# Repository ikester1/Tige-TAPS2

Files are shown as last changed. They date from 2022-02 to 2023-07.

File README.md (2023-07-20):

# Replacement Tige TAPS Trim Controller

This is a replacement for the original trim controller for an early 2000's [Tige](https://www.tige.com/) 22v wakeboard boat.
The *electric actuator* is made by [Lenco](https://www.lencomarine.com), the Tige logo'd
trim indicator gauge is probably made by [Faria](https://fariabeede.com), and the
"black box" controller is under the dashboard.  The "black box" takes the trim switch input and drives the actuator
and gauge.  Coupled with a plate on the transom, Tige called the entire system **TAPS2**.

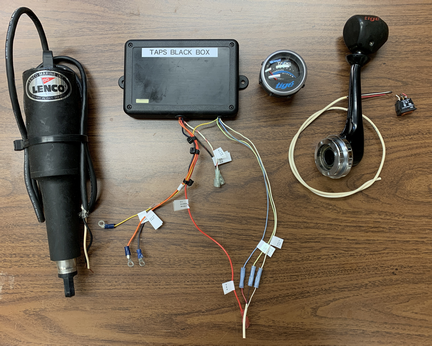
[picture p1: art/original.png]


The original controller is prone to failure, and is no longer available from Lenco or Tige.  There are
other solutions from Lenco but there are none which retain the use of the original trim switch and Tige
gauge.

Tige's TAPS controller fully retracts the actuator at each start so one must
reposition the trim at every restart.
This project improves on the original implementation by saving the final actuator position for the next
restart.
If everything works right, the trim will not move and the gauge will be correctly positioned when the
boat is restarted.

The controller's external connections are power and ground, trim switch top/middle/bottom,
gauge power/ground/signal, and two actuator motor power leads.  The controller box has a lighted
setup pushbutton and redundant trim switch.
The box, while deeper than the original controller, has the same footprint.

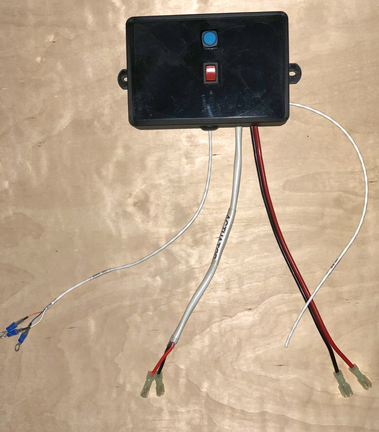
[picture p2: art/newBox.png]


This project includes the controller's schematic diagram and PCB layout, a 3D printable enclosure, and the C++
controller software.  With access to a 3D printer, the cost of the controller should be less than $75.

# Making the Controller

The replacement controller is a custom processor board connected to a commercial
[H-Bridge](https://en.wikipedia.org/wiki/H-bridge)
to switch the relatively high current actuator connections.
The processor board holds a [Raspberry Pi Pico](https://www.google.com/search?q=raspberry+pico) and surrounding
glue circuitry.

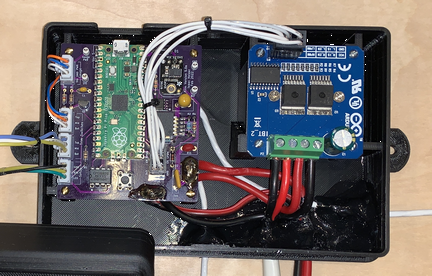
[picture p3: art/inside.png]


## Processor Board

The [pcb](pcb) directory holds the [KiCad 6](https://www.kicad.org/) files detailing the schematic and
printed circuit layout, and
[bin/TAPS.zip](bin)
is a
[Gerber](https://en.wikipedia.org/wiki/Gerber_format)
file to send to a printed circuit board
fabricator such as [OSHPARK](https://oshpark.com/).

Almost all components are available at [Digi-Key](https://www.digikey.com/) and the schematic is annotated with
manufacturer and product numbers for each component.
The Pico power supply is from [adafruit](https://www.adafruit.com/product/4683).
In addition to the usual soldering supplies, a special crimper
( [Amazon](https://www.amazon.com/dp/B088NQV8Z3) )
is needed for the board's connectors though
one could skip the connectors and solder the wires to the boards.

## H-Bridge

The commercial H-Bridge is a BTS7960 43A High Power Motor Driver Module and can be purchased on Amazon for less than $10 from
[several souces](https://www.amazon.com/s/?url=search-alias%3Daps&field-keywords=BTS7960+43A+Motor+Driver+Module).
The H-Bridge board has an 8 pin header for its logic connections to the processor board; replace this header with the same locking connector
as the processor board to improve robustness.

## Code

The C++ code is compiled on Linux with the [Raspberry Pi Pico C/C++ SDK](https://datasheets.raspberrypi.com/pico/raspberry-pi-pico-c-sdk.pdf).
Go to the [src](src) directory, type `cmake -B build` followed by `cd build && make` to generate the executable to
copy to the Pico processor as described in the SDK. The most recent executable is [bin/taps.elf](bin).

## Enclosure and Switches

The [box](box) directory holds the [SketchUp](https://www.sketchup.com/) enclosure design files.
[Cura](https://ultimaker.com/software/ultimaker-cura) successfully slices
[bin/boxBottom.stl](bin) and [bin/boxTop.stl](bin)
for an [Ultimaker 3D printer](https://ultimaker.com/) though other slicers and printers should work.
The ABS enclosure's bottom secures the boards and external wires with 2-56 screws, while the top holds the setup button and
auxiliary trim switch.
The auxiliary trim switch is a duplicate of the button used on the throttle of the Tige boat.
It is manufactured by
[E-Switch](https://www.e-switch.com/),
part number
R1966IBLKREDEF,
and available on
[Digi-Key](https://www.digikey.com/short/t0br9zjr)
as part number [EG5445-ND](https://www.digikey.com/short/t0br9zjr).
The 16mm illumated setup pushbutton is available from [adafruit](https://www.adafruit.com/product/1477)
and [amazon](https://www.amazon.com/dp/B0148183D2).

The box top and bottom are held together with two 6.3mm automotive plastic trim fasteners.

## Connections

Connect the three *gauge* wires to the existing Tige TAPS gauge -- these should be the only wires connected to
the gauge terminal posts.  This new black box supplies power to the gauge; **do not** also connect the gauge's power terminal to
the boat's electrical system.  Looking from the rear, the black box gauge *PWR* leads goes on the right, *GND* goes in the middle,
and *SIG* goes on the left.  **Connecting any power lead to the gauge's *SIG* terminal will damage the gauge.**
The spade terminal near the blue cap is for gauge illumination and this connection should go to the lighting circuit
shared with the other instruments.

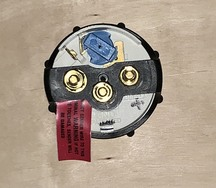
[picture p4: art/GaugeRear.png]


Connect the black box's two actuator leads to the two leads coming from the Lenco electric actuator.  Polarity
is only important when it comes time to ensure the actuator retracts when the black box thinks it should be
retracting, and extends when the black box thinks it is extending the actuator.  If you get the leads backwards,
they can simply be plugged in the other way.

Connect the three trim switch wires to the boat's trim switch ... on my boat this switch is on the throttle handle.
There is no appreciable current flowing through the trim switch so any secure means of connection (any kind of connector)
should be fine.  Do not otherwise connect the boat's power or ground to these connections.

Finally, connect the black box's power and ground to the electrical system.  The heavy power lead should be connected, most likely,
to the same 15A breaker that was powering the original black box (actually, a 10A breaker is probably adequate).
The other, lighter, power lead should be connected to a switched power source.

# Setup

The black box has a *setup mode* entered by pressing its pushbutton.  The button's LED pulses
when the box is in *setup mode* and goes dark when *setup mode* is exited.  *Setup mode* is automatically exited after one
minute of inactivity, or if the pushbutton is pressed and held for at least two seconds.

As soon as *setup mode* is entered, the actuator should fully retract.
If the actuator extends instead of retracts, simply reverse the actuator leads and try again.
When not in
*setup mode*, pressing the side
of the rocker switch nearest the pushbutton should extend the actuator, the other side of
the rocker switch should retract it.
Similarly, pressing the top of the rocker switch on the throttle should extend the actuator and the bottom half of the
switch should retract it.  Something is wrong with the
throttle's switch or wiring if the box's rocker switch works but the throttle's does not.

The primary purpose of *setup mode* is to calibrate the TAPS gauge.
This is done by manually setting the gauge's fully retracted (wakeboard) and 25% - 50% - 75% - 100% 
extended (slalom) gauge needle positions.
More specifically, the gauge's 8, 6, 4, 2, and 0 readings are adjusted.
Enter *setup mode* to adjust these positions and use the trim switch to set the needle's **8** position.
Press the setup button and set the needle's **6** position.
Press the button and set the **4** position; continue for the **2** and **0** positions.
One should be careful when setting the **0** position: release the trim switch as soon as the
**0** position is reached (do not linger) as doing otherwise will bias the box's idea of when **0** was reached.
*Setup mode* automatically exits once the setup button is pressed after adjusting for the **0** position.

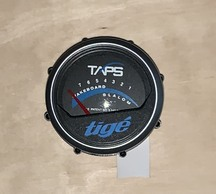
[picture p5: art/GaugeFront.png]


# Operation

The trim switch and TAPS system should operate exactly as the original system, except:
- The new black box remembers the actuator and gauge positions when the boat is shut down.
The original box retracts the actuator and resets the gauge at every boat restart.

- The original black box runs the actuator as long as the trim switch is pressed; this replacement box stops the actuator
once it is 50% beyond the retract or extend limits.
In any case, running the Lenco actuator beyond its limits causes no harm to the actuator.

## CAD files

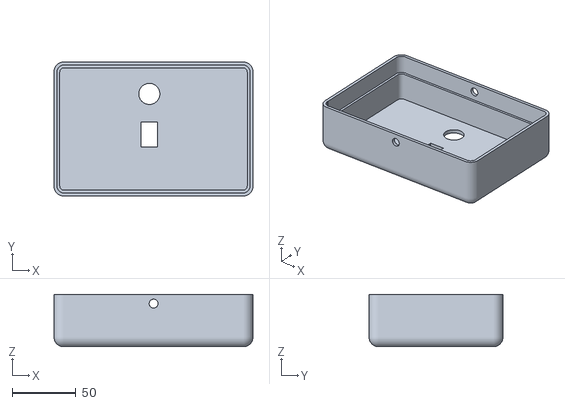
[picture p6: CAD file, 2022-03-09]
bin/boxTop.stl
156.0 x 105.0 x 41.1

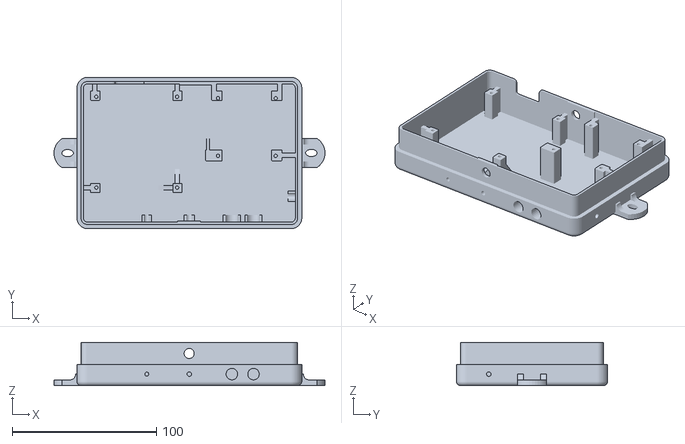
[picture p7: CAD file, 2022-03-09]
bin/boxBottom.stl
187.9 x 105.0 x 30.0

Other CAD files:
box/box.skp

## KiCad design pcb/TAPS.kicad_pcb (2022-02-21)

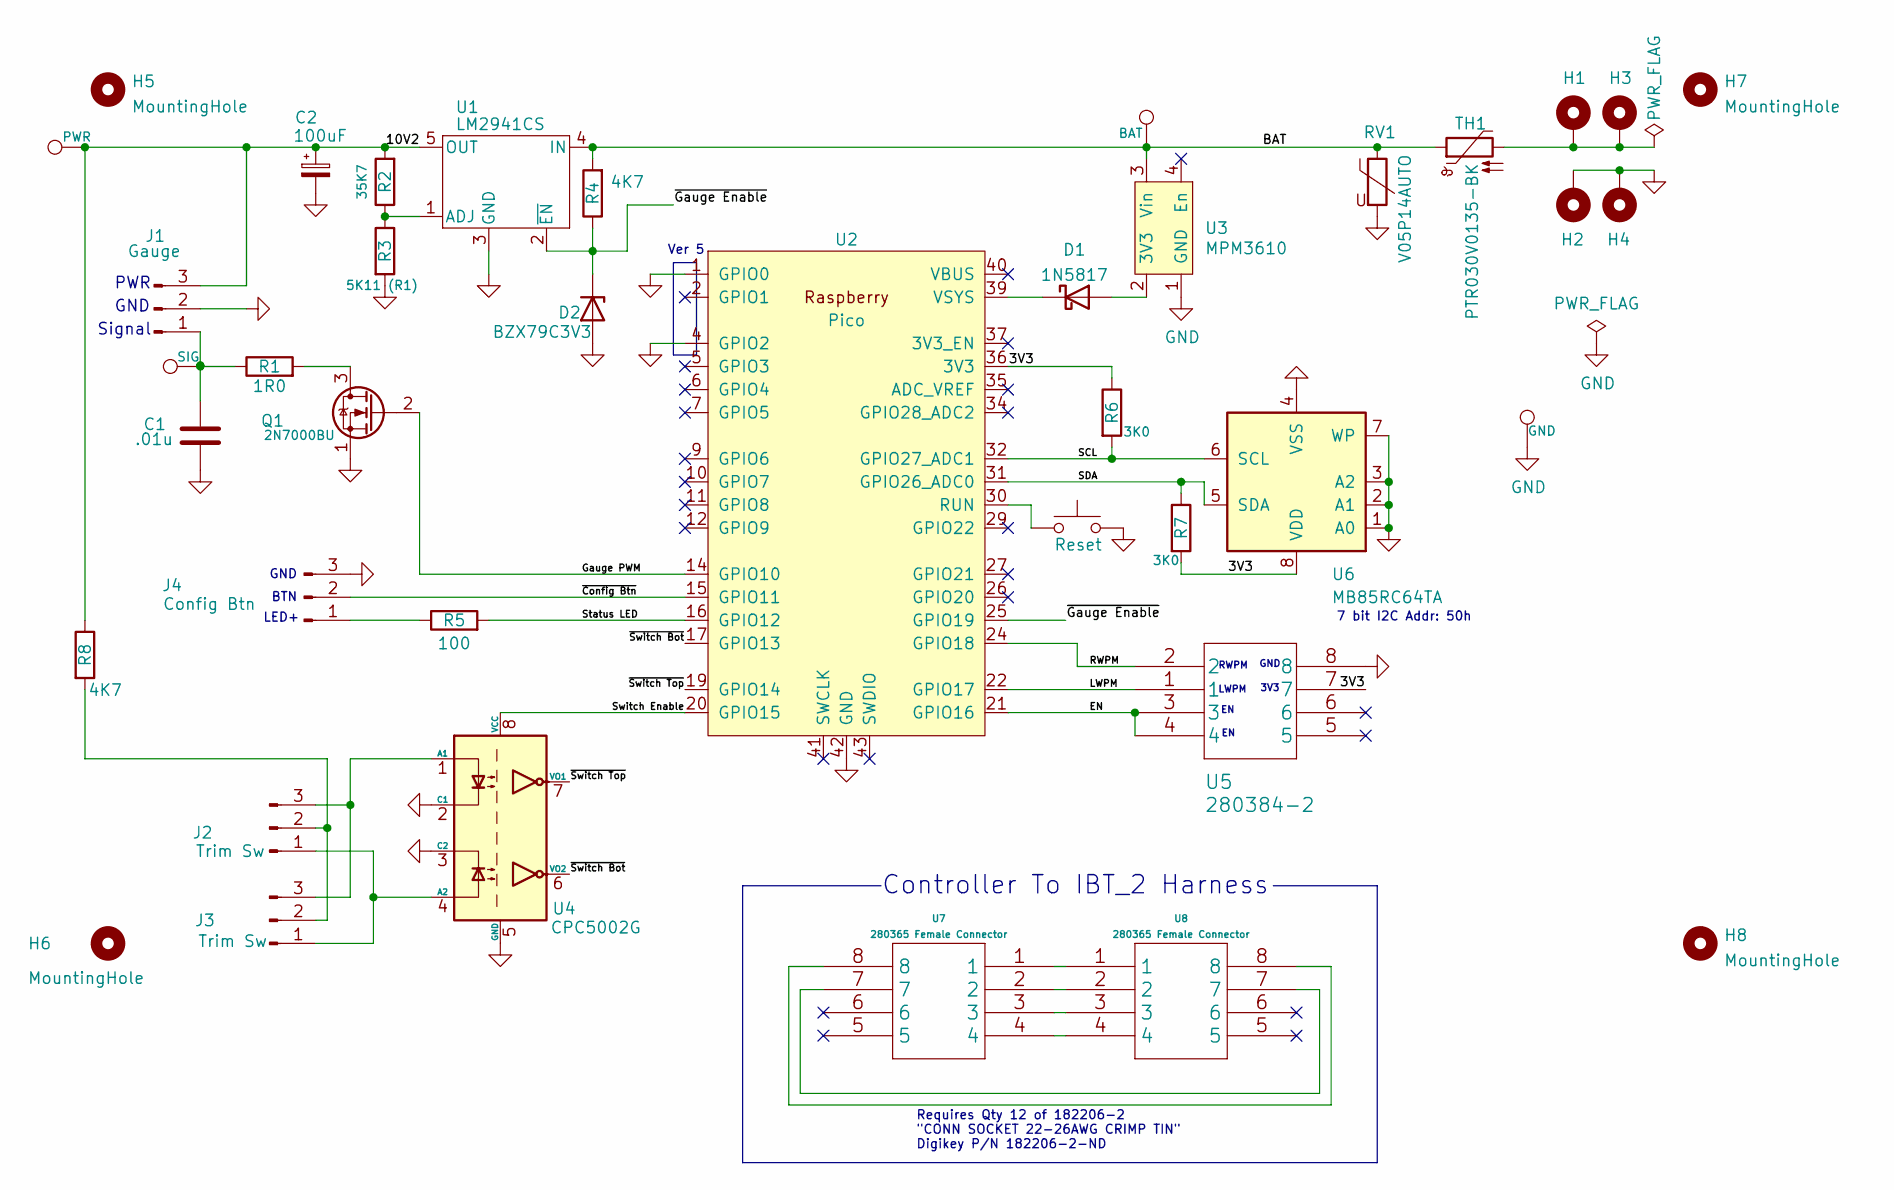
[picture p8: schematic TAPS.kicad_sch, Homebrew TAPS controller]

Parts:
C1: .01u; C_Disc_D4.3mm_W1.9mm_P5.00mm; Digikey PN 399-4206-ND
C2: 100uF; C_Disc_D9.0mm_W5.0mm_P5.00mm; Digikey PN 478-1847-ND
D1: 1N5817; D_A-405_P7.62mm_Horizontal; Digikey PN 1N5817RLGOSCT-ND
D2: BZX79C3V3; D_DO-34_SOD68_P7.62mm_Horizontal; Digikey PN BZX79C3V3-ND
H1, H2, H3, H4: MountingHole_Pad; MountingHole_2.5mm_Pad_TopBottom
H5, H6, H7, H8: MountingHole; MountingHole_2.5mm
J1: Gauge; JST_XH_B3B-XH-A_1x03_P2.50mm_Vertical; Digikey PN 455-1990-ND
J2, J3: Trim Sw; JST_XH_B3B-XH-A_1x03_P2.50mm_Vertical; Digikey PN 455-1990-ND
J4: Config Btn; JST_XH_B3B-XH-A_1x03_P2.50mm_Vertical
Q1: 2N7000BU; TO-92_Inline; Digikey PN 2N7000BU-ND
R1: 1R0; R_Axial_DIN0204_L3.6mm_D1.6mm_P7.62mm_Horizontal; Digikey PN CF18JT1R00CT-ND
R2: 35K7; R_Axial_DIN0204_L3.6mm_D1.6mm_P7.62mm_Horizontal; Digikey PN RNF18FTD35K7CT-ND
R3: 5K11 (R1); R_Axial_DIN0204_L3.6mm_D1.6mm_P7.62mm_Horizontal; Digikey PN 738-RNF18FTD5K11CT-ND
R4, R8: 4K7; R_Axial_DIN0204_L3.6mm_D1.6mm_P7.62mm_Horizontal; Digikey PN CF18JT4K70CT-ND
R5: 100; R_Axial_DIN0204_L3.6mm_D1.6mm_P7.62mm_Horizontal; Digikey PN CF18JT100RCT-ND
R6, R7: 3K0; R_Axial_DIN0204_L3.6mm_D1.6mm_P7.62mm_Horizontal; Digikey PN CF18JT3K00CT-ND
RV1: V05P14AUTO; C_Disc_D7.5mm_W5.0mm_P5.00mm; Digikey PN F6411-ND
SW1: Reset; SW_PUSH_6mm_H7.3mm; Digikey PN 450-1650-ND
TH1: PTR030V0135-BK; C_Disc_D10.0mm_W2.5mm_P5.00mm; Digikey PN PTR030V0135-BK-ND
TP1: PWR; TestPoint_Keystone_5000-5004_Miniature; Digikey PN 36-5002-ND
TP2: BAT; TestPoint_Keystone_5000-5004_Miniature; Digikey PN 36-5002-ND
TP3: GND; TestPoint_Keystone_5000-5004_Miniature; Digikey PN 36-5002-ND
TP4: SIG; TestPoint_Keystone_5000-5004_Miniature; Digikey PN 36-5002-ND
U1: LM2941CS; TO-263-5_TabPin3; Digikey PN LM2941CS-ND
U2: Pico; RPi_Pico_SMD; Digikey PN 2648-SC0915CT-ND
U3: MPM3610; Converter_DCDC_Adafruit_MPM3610
U4: CPC5002G; DIP-8_W7.62mm; Digikey PN CLA383-ND
U5: 280384-2; Connector_TE_280384-2; Digikey PN A106409-ND
U6: MB85RC64TA; SOP-8_3.9x4.9mm_P1.27mm; Digikey PN 865-1274-1-ND
U7, U8: 280365 Female Connector; Digikey PN A121748-ND

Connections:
/3V3: R6.1, R7.2, U2.36 (3V3), U5.7, U6.8 (VDD)
/10V2: C2.1, J1.3, R2.2, R8.1, TP1.1, U1.5 (OUT)
/BAT: R4.2, RV1.1, TH1.1, TP2.1, U1.4 (IN), U3.3 (Vin)
/EN: U2.21 (GPIO16), U5.3, U5.4
/Gauge PWM: Q1.2 (G), U2.14 (GPIO10)
/LWPM: U2.22 (GPIO17), U5.1
/RWPM: U2.24 (GPIO18), U5.2
/SCL: R6.2, U2.32 (GPIO27_ADC1), U6.6 (SCL)
/SDA: R7.1, U2.31 (GPIO26_ADC0), U6.5 (SDA)
/Status LED: R5.2, U2.16 (GPIO12)
/Switch Enable: U2.20 (GPIO15), U4.8 (VCC)
/~Config Btn: J4.2, U2.15 (GPIO11)
/~Gauge Enable: D2.1 (K), R4.1, U1.2 (~EN), U2.25 (GPIO19)
/~Switch Bot: U2.17 (GPIO13), U4.6 (VO2)
/~Switch Top: U2.19 (GPIO14), U4.7 (VO1)
GND: C1.2, C2.2, D2.2 (A), H2.1, H4.1, J1.2, J4.3, Q1.1 (S), R3.2, RV1.2, SW1.2, TP3.1, U1.3 (GND), U2.1 (GPIO0), U2.3 (GND), U2.4 (GPIO2), U2.8 (GND), U2.13 (GND), U2.18 (GND), U2.23 (GND), U2.28 (GND), U2.33 (GND), U2.38 (GND), U2.42 (GND), U3.1 (GND), U4.2 (C1), U4.3 (C2), U4.5 (GND), U5.8, U6.1 (A0), U6.2 (A1), U6.3 (A2), U6.4 (VSS), U6.7 (WP)
unnamed: C1.1, J1.1, R1.1, TP4.1
unnamed: D1.1 (K), U2.39 (VSYS)
unnamed: D1.2 (A), U3.2 (3V3)
unnamed: H1.1, H3.1, TH1.2
unnamed: J2.1, J3.1, U4.4 (A2)
unnamed: J2.2, J3.2, R8.2
unnamed: J2.3, J3.3, U4.1 (A1)
unnamed: J4.1, R5.1
unnamed: Q1.3 (D), R1.2
unnamed: R2.1, R3.1, U1.1 (ADJ)
unnamed: SW1.1, U2.30 (RUN)
unnamed: U7.1, U8.1
unnamed: U7.2, U8.2
unnamed: U7.3, U8.3
unnamed: U7.4, U8.4
unnamed: U7.7, U8.7
unnamed: U7.8, U8.8

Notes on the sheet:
Signal
3V3
7 bit I2C Addr: 50h
RWPM
BTN
Requires Qty 12 of 182206-2 "CONN SOCKET 22-26AWG CRIMP TIN" Digikey P/N 182206-2-ND
GND
Ver 5
LED+
LWPM
Controller To IBT_2 Harness
PWR

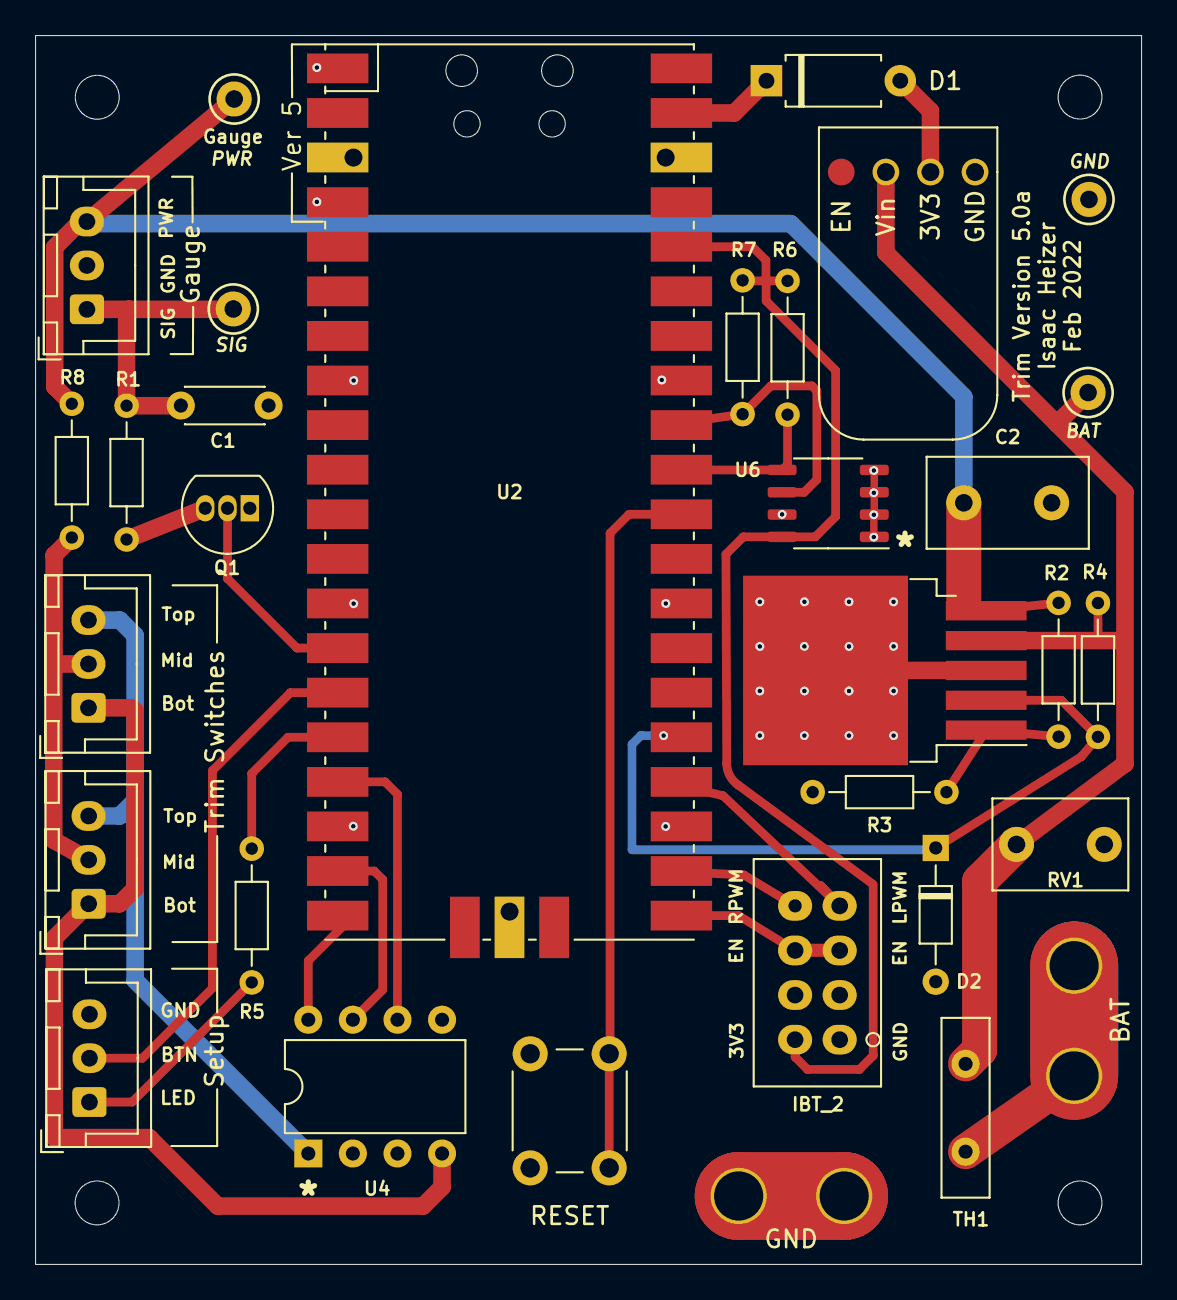
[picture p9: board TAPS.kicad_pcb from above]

Board: 2 copper layers, 63.0 x 70.0 mm, 38 parts (0 on the bottom side), 27 nets.

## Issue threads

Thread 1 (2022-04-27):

Bottom Silkscreen

matthewmooney, 2022-04-27:
Thank you for putting this together!  Exactly what I need for my 04 Tige 24V.  Attempting to get the board printed with OSHPark but I keep getting an error that the zip file is missing the bottom silkscreen.

ikester1, 2022-04-27:
There is no bottom silkscreen!  OSH used to be OK with that….

I made three extra units.  I’ll send you one for $50 to cover costs and
labor if you want.  Buyer beware, though!

Mooney pilot?  I built and flew a Lancair

On Wed, Apr 27, 2022 at 12:28 PM matthewmooney ***@***.***>
wrote:

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
--
Sent from my iPad

matthewmooney, 2022-04-28:
There might be a way to navigate it but I figured I would start by seeing if maybe it got left out on accident.  If you have a completed board i would gladly take that off your hands.   It would save me a lot of headaches! 

Unfortunately no just the last name,   however I'm hoping to go back to school to become a pilot in the fall. 

⁣Get BlueMail for Android

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

Closed 2023-07-10.

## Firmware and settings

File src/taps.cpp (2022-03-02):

#include <stdio.h>
#include <memory.h>
#include "pico/stdlib.h"

#include <cmath>

#include "config.h"
#include "util.hpp"
#include "CGauge.hpp"
#include "CNVFlash.hpp"
#include "CNVFRAM.hpp"
#include "taps.hpp"
#include "CActuator.hpp"
#include "CPowerFail.hpp"

void configure( CNVState&, CLED& statusLED, CButton& button, CSPDT& trimSwitch, CActuator&, CGauge& );
void demoMode( CGauge&, CButton& stopButton );
void doCommand( int ch, CNVState& );

static CNVState& findNVResource() {
    static CNVFRAM nvFRAM( I2C_ADDR::FRAM, BoardPin::FRAM_SDA );
    if( nvFRAM.size() > 0 )
        return nvFRAM;

    static CNVFlash nvFlash;
    return nvFlash;
}

int main()
{
    stdio_init_all();

    CNVState&   nvState = findNVResource();
    CLED        picoLED( BoardPin::STANDARD_LED );
    CLED        statusLED( BoardPin::STATUS_LED );
    CPowerFail  powerFail;
    CActuator   actuator( ACTUATOR_FULL_TRANSIT_MS );
    CGauge      gauge( nvState.gaugeCal().get(), GAUGE_PWM_FREQ );

    bool        movedTrimSinceLastSave = false;
    int         numberOfTrimMovements  = 0;

    //
    // This object posts "TRIM_SWITCH_xxx" messages as the trim switch is manipulated
    //
    class trimSwitch : public CSPDT {
        typedef CSPDT   super;
        CGPIO_OUT       m_switchEnable;     //  Must be set to output high on boards with optical switch isolators
    public:
        trimSwitch() :
        super( BoardPin::TRIM_SWITCH_EXTEND, BoardPin::TRIM_SWITCH_RETRACT ),
        m_switchEnable( BoardPin::TRIM_SWITCH_ENABLE )
        {
            m_switchEnable.setOn();
        }

        void onTop(bool pressed) {
            if( auto msg = CMessage::alloc( pressed ? CMessage::Type::TRIM_TOP_ON : CMessage::Type::TRIM_OFF ) )
                msg->push();
        }
        void onBottom(bool pressed) {
            if( auto msg = CMessage::alloc( pressed ? CMessage::Type::TRIM_BOTTOM_ON : CMessage::Type::TRIM_OFF ) )
                msg->push();
        }
    } spdt;

    //
    // This object posts a "CONFIG_BUTTON_ON" message when the configure pushbutton is pressed
    //
    class ConfigButton : public CButton {
        typedef     CButton super;
        bool        m_messages;
    public:
        ConfigButton() : super( BoardPin::CONFIG_PUSHBUTTON ), m_messages( false )  {}
        void onChange( bool b ) override {
            if( b && m_messages )
                if( auto msg = CMessage::alloc( CMessage::Type::CONFIG_BUTTON_ON ) )
                    msg->push();
        }
        void enableMessages()       { super::enable(); m_messages = true; }
        void disableMessages()      { m_messages = false; }
    } configButton;
    configButton.enable();          // no messages yet

    //
    // This object posts a "HEARTBEAT" message once per second, and blinks the pico led
    //
    class heartBeat {
        struct myTick : public CGlobalTimer::COnTick {
            heartBeat &m_me;
            void onTick() override                      { m_me.onTick(); }
            myTick( heartBeat &m ) : m_me( m )          {}
        } m_myTick;

        const int   m_interval;
        int         m_count;
        CLED        &m_led;                 // LED to toggle every m_interval
        bool        m_msg;                  // should we send message at m_interval?

    public:
        heartBeat( int interval, CLED& led ) : m_myTick(*this), m_interval( interval ), m_count(0), m_led(led), m_msg(false) {}
        void onTick()           {   if( --m_count <= 0 ) {
                                        m_led.toggle();
                                        m_count = m_interval;
                                        if( m_msg )
                                            if( auto msg = CMessage::alloc( CMessage::Type::HEARTBEAT ) )
                                                msg->push();
                                    }
        
                                };

        bool enableMessages()           { auto oval = m_msg; m_msg = true; m_myTick.start(); return oval; }
        bool disableMessages()          { auto oval = m_msg; m_msg = false; return oval; }

    } heartBeat( 1000/CGlobalTimer::msPerTick(), picoLED );

    gauge.enable();

    if( configButton.strobe() == true ) {
        //
        // Config button is pressed during power up....enter demo mode which sweeps the gauge dial
        //
        configButton.waitForPressed();
        demoMode( gauge, configButton );
    }

    float recoveredActuatorPercent = NAN;
    if( nvState.reason().wasValid() && nvState.actuatorPercent().wasValid() ) {
        if( nvState.reason().get() == CNVState::PowerDownSave || nvState.reason().get() == CNVState::SavedPositionImmediate ) {
            //
            // We were able to save and recover the last actuator postion, so we assume it is still at that position.
            //   All we need to do is let the actuator know where it is
            //
            recoveredActuatorPercent = nvState.actuatorPercent().get();
            actuator.setAlreadyAtPercent( recoveredActuatorPercent );
            spdt.enable();
            configButton.enableMessages();
            gauge.setSlow( 100 );
        }
    }

    if( isnan( recoveredActuatorPercent ) ) {
        //
        // Don't know where the actuator is/was, so best we can do is reset it
        //
	    actuator.startFullRetract();
    }

    heartBeat.enableMessages();
    gauge.setSlow( actuator.percent() );

    while (true) {
        auto msg = CMessage::pop();
        if( msg == nullptr ) {
            if( int ch = getchar_timeout_us(0); ch != PICO_ERROR_TIMEOUT ) {
                if( actuator.active() == false ) {
                    if( msg = CMessage::alloc( CMessage::Type::USER_COMMAND, ch ); msg != nullptr )
                        msg->push();
                }
                continue;
            }
            __wfi();
            continue;
        }

        switch( msg->type() ) {
        case CMessage::Type::TRIM_TOP_ON:
            movedTrimSinceLastSave = true;
            ++numberOfTrimMovements;
            statusLED = true;
            actuator.retract();
            configButton.disableMessages();
            break;

        case CMessage::Type::TRIM_BOTTOM_ON:
            movedTrimSinceLastSave = true;
            ++numberOfTrimMovements;
            statusLED = true;
            actuator.extend();
            configButton.disableMessages();
            break;

        case CMessage::Type::TRIM_OFF:
            statusLED = false;
            actuator.stop();
            gauge.set( actuator.percent() );

            if( nvState.unlimitedUpdates() ) {
                nvState.setActuatorPercent( actuator.percent(), CNVState::SavedPositionImmediate ).commit();
                movedTrimSinceLastSave = false;
            } else if( numberOfTrimMovements == 1 ) {
                nvState.setActuatorPercent( actuator.percent(), CNVState::InitialMovement ).commit();
            }

            configButton.enableMessages();
            break;

        case CMessage::Type::USER_COMMAND:
        case CMessage::Type::CONFIG_BUTTON_ON:
            configButton.disableMessages();
            heartBeat.disableMessages();
            CMessage::flush();
            statusLED = true;

            if( msg->type() == CMessage::Type::CONFIG_BUTTON_ON )
                configure( nvState, statusLED, configButton, spdt, actuator, gauge );
            else
                doCommand( msg->data(), nvState );

            statusLED = false;
            CMessage::flush();
            configButton.enableMessages();
            heartBeat.enableMessages();
            break;

        case CMessage::Type::GAUGE_UPDATE:
            { const auto percentUnbounded = actuator.percentUnbounded();
                if( percentUnbounded < -50 || percentUnbounded > 150 ) {
                    statusLED = false;
                    actuator.stop();
                }
            }
            gauge.set( actuator.percent() );
            break;

        case CMessage::Type::FULL_RETRACT:
            statusLED = true;
            if( actuator.activeTime() >= actuator.targetRullRetractRunTime() ) {
                actuator.stop();
                sleep_ms( 100 );
                if( nvState.reason().get() == CNVState::SavedPositionLazy && !nvState.closeEnough( actuator.percent() ) ) {
                        gauge.setSlow( actuator.percent() );
                        if( nvState.actuatorPercent().get() >= 0 && nvState.actuatorPercent().get() <= 100 ) {
                            actuator.extend( false );
                            for( auto pct = actuator.percent(); !nvState.closeEnough(pct) && pct < nvState.actuatorPercent().get(); pct = actuator.percent() )
                                gauge.set( pct );
                            actuator.stop();
                        }
                }
                gauge.setSlow( actuator.percent() );
                statusLED = false;
                spdt.enable();
                msg->flush();
                configButton.enableMessages();
            } else {
                //
                // We want a sweep of the TAPS gauge while the actuator is doing its initial retraction
                //
                const static auto ticksForRetract = float( actuator.targetRullRetractRunTime() ) / actuator.msPerGaugeTick();
                const static auto deltaPercentPerTick = 2 * (100 / ticksForRetract);
                static bool gaugeSweepIncreasing = true;

                auto currentGauge = gauge.get();
                if( currentGauge >= 99 )
                    gaugeSweepIncreasing = false;
                else if( currentGauge <= 1 )
                    gaugeSweepIncreasing = true;

                gauge.set( currentGauge + (gaugeSweepIncreasing ? deltaPercentPerTick : -deltaPercentPerTick) );
            }
            break;

        case CMessage::Type::HEARTBEAT:
            if( nvState.unlimitedUpdates() == false && !powerFail.available() && spdt == false ) {
                if( movedTrimSinceLastSave && actuator.secondsSinceLastStop() >= ACTUATOR_POSITION_SAVE_DELAY_SEC ) {
                    movedTrimSinceLastSave = false;
                    if( !nvState.closeEnough( actuator.percent() ) ) {
                        statusLED.toggle();
                        nvState.setActuatorPercent( actuator.percent(), CNVState::SavedPositionLazy ).commit();
                        sleep_ms(100);
                        statusLED.toggle();
                    }
                }
            }
            break;

        case CMessage::Type::POWER_FAILED:
            actuator.stop();
            gauge.disable();
            printf( "*** POWER FAILURE ***\n");
            configButton.disableMessages();
            heartBeat.disableMessages();
            CMessage::flush();
            picoLED = true;
            statusLED = true;
            if( movedTrimSinceLastSave ) {
                nvState.setActuatorPercent( actuator.percent(), CNVState::PowerDownSave ).commit();
                movedTrimSinceLastSave = false;
                numberOfTrimMovements = 0;
            }
            break;

        case CMessage::Type::POWER_RESTORED:
            printf( "*** POWER RESTORED ***\n" );
            statusLED = false;
            picoLED = false;
            {
                auto currentGauge = gauge.get();
                gauge.set(0).enable().setSlow( currentGauge );
            }
            configButton.enableMessages();
            heartBeat.enableMessages();
            break;

        default:
            msg->print();
            break;
        }
        msg->free();
    }
    return 0;       // never gets here, but...
}

//
// We use the trim switch to set the 0, 25, 50, 75, and 100% points on the gauge.  We use
// the button presses to move to the next percentile.
//
// If the user presses and holds the config button, we abort
//
// If the user doesn't do anything for CONFIG_INACTIVITY_ABORT_SEC seconds, we abort
//
void calibrateGauge( CNVState& nvState, CButton& button, CSPDT& trimSwitch, CGauge& gauge ) {
    CGauge::calType_t gaugeCal( nvState.gaugeCal().get() );

    nvState.print();
    gauge.setCurrentDutyCycleSlow( gaugeCal[0] );
    button.waitForReleased();

    uint slotNumber = 0;
    auto lastActivityTime = get_absolute_time();

    while( absolute_time_diff_us( lastActivityTime, get_absolute_time() ) / 1000000 < CONFIG_INACTIVITY_ABORT_SEC ) {

        while( trimSwitch.bottom() ) {
            gauge.setCurrentDutyCycle( gauge.currentDutyCycle() - 0.25f );
            sleep_ms( 25 );
            lastActivityTime = get_absolute_time();
        }
        while( trimSwitch.top() ) {
            gauge.setCurrentDutyCycle( gauge.currentDutyCycle() + 0.25f );
            sleep_ms( 25 );
            lastActivityTime = get_absolute_time();
        }
        if( button.pressed() ) {
            if( button.waitForReleased( CONFIG_ABORT_MS ) == false ) {
                //
                // Button is being held down.....abort!
                //
                return;
            }

            gaugeCal[ slotNumber ] = gauge.currentDutyCycle();
            printf("  PWM[%d] = %.2f%%\n", slotNumber, gaugeCal[ slotNumber ] );
            if( ++slotNumber >= gaugeCal.size() )
                break;

            lastActivityTime = get_absolute_time();
        }
        __wfi();
    }

    if( !gauge.isValidCalibration( gaugeCal ) ) {
        printf( "\n** REJECTED!\n");
        return;
    }

    nvState.setGaugeCal( gaugeCal ).commit();
    gauge.calibrate( gaugeCal );
}

//
// Make the status LED pulsate and let the user calibrate the trim gauge.  Retract the actuator along
//   the way to allow the user to verify the actuator leads are correct (i.e. they may be reversed)
//
void configure( CNVState& nvState, CLED& statusLED, CButton& button, CSPDT& trimSwitch, CActuator& actuator, CGauge& gauge ) {
    const auto initialActuatorPercent = actuator.percent();
    {
        //
        // Fully retract the actuator so the owner can know the motor is hooked up right
        //
        actuator.startFullRetract(false);
        while( actuator.activeTime() < actuator.targetRullRetractRunTime() )
            ;
        actuator.stop();

        //
        // Let the owner adjust the gauge settings
        //
        CPWM statusPWM( statusLED, 1000 );
        CPWMCycler ledCycler( statusPWM, 2 );
        ledCycler.setPercents( 5, 100 ).enable();
        calibrateGauge( nvState, button, trimSwitch, gauge );
    }
    statusLED = false;

    //
    // Restore the actuator to its initial position
    //
    if( actuator.percent() != initialActuatorPercent ) {
        actuator.extend( false );
        while( actuator.percent() < initialActuatorPercent )
            ;
        actuator.stop();
    }

    //
    // Set the gauge to the actuator position
    //
    gauge.setSlow( actuator.percent() );

    button.waitForReleased();
}

//
// Enter "demo mode".  Demo mode continuously sweeps the gauge dial until the stop button is pressed
//
void demoMode( CGauge& gauge, CButton& stopButton ) {
    auto origPercent = gauge.enable().get();
    {
        CPWMCycler cycler( gauge.pwm(), 1.5*ACTUATOR_FULL_TRANSIT_MS/1000.0 );
        cycler.setPercents( gauge.getLowPercent(), gauge.getHighPercent() ).enable();

        while( !stopButton.released() )
            __wfi();
        while( !stopButton.pressed() )
            __wfi();
    }
    gauge.setSlow( origPercent );
    stopButton.waitForReleased();
}

void doCommand( int cmd, CNVState& nvState ) {
    if( cmd != '\r' ) {
        switch( cmd = tolower(cmd) ) {
        case 'z':               // zap the NV state
            if( areYouSure( "\nErase all remembered settings...") ) {
                nvState.zap();
                printf( "\nzapped!\n");
            }
            break;

        case 'p':               // print the non-volatile storage state
            nvState.print();
            break;

        default:              // fool with nonvolatile's i2c
            if( !nvState.doCommand( cmd ) )
                putchar('?');
            break;
        }
    }
    printf("\n> ");
}

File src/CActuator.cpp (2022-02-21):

#include <stdio.h>
#include "pico/stdlib.h"

#include "config.h"
#include "util.hpp"
#include "taps.hpp"
#include "CActuator.hpp"

static constexpr int ENABLE_DELAY_MS = 20;

CActuator::CActuator( int fullTransitMs ) :
	m_MOTOR_ENABLE( BoardPin::MOTOR_ENABLE ),
	m_LPWM( BoardPin::MOTOR_LPWM ),
	m_RPWM( BoardPin::MOTOR_RPWM ),

	m_fullTransitMs( fullTransitMs ),
	m_fullTransitMsToBeSure( (11*fullTransitMs)/10 ),
    m_moved( false ),
	m_currentDirection( 0 )

{
	stopMotion();
}

void CActuator::setMoved( bool moved ) {
    m_moved = moved;
}

//
// Low level start extending the actuator
//
void CActuator::startExtendMotion() {
	m_MOTOR_ENABLE = false;
	if( ENABLE_DELAY_MS )
		sleep_ms( ENABLE_DELAY_MS );
	m_LPWM = false;
	m_RPWM = true;
	m_MOTOR_ENABLE = true;
	m_currentDirection = 1;
    setMoved( true );
}

//
// Low level start retracting the actuator
//
void CActuator::startRetractMotion() {
	m_MOTOR_ENABLE = false;
	if( ENABLE_DELAY_MS )
		sleep_ms( ENABLE_DELAY_MS );
	m_RPWM = false;
	m_LPWM = true;
	m_MOTOR_ENABLE = true;
	m_currentDirection = -1;
    setMoved( true );
}

//
// Low level stop moving the actuator
//
void CActuator::stopMotion() {
	m_MOTOR_ENABLE = false;
	m_LPWM = m_RPWM = false;
	m_MOTOR_ENABLE = true;			// brake
	m_currentDirection = 0;
}

void CActuator::extend( bool updateGauge ) {
	m_lastStopTime.clear();
	startExtendMotion();
	m_startTime.setNow();
	if( updateGauge )
		m_gaugeUpdater.start();
}

void CActuator::retract( bool updateGauge ) {
	m_lastStopTime.clear();
	startRetractMotion();
	m_startTime.setNow();
	if( updateGauge )
		m_gaugeUpdater.start();
}

void CActuator::startFullRetract( bool updateGauge ) {
	m_lastStopTime.clear();
	m_currentPositionMs = 0;
	startRetractMotion();
	m_startTime.setNow();

	if( updateGauge )
		m_gaugeUpdater.start( CMessage::Type::FULL_RETRACT );
}

void CActuator::stop() {
	if( !active() )
		return;

	const bool retracting = (m_currentDirection < 0);

	stopMotion();
	auto runTime = m_startTime.ms();

	m_lastStopTime.setNow();

	m_currentPositionMs += retracting ? -runTime : runTime;
	m_currentPositionMs = MAX( m_currentPositionMs, 0 );
	m_currentPositionMs = MIN( m_currentPositionMs, m_fullTransitMs );

	m_startTime.clear();
	m_gaugeUpdater.stop();

	printf("Actuator Stop: %d mS, %.2f%%\n", m_currentPositionMs, percent() );
}

int CActuator::secondsSinceLastStop() const {
	return m_lastStopTime.ms() / 1000;
}

float CActuator::percentUnbounded() const {
	int position = m_currentPositionMs;
	if( active() )
		position += (m_currentDirection < 0) ? -m_startTime.ms() : m_startTime.ms();
	float unboundedPercent =  (position*100.0f) / m_fullTransitMs;
	return unboundedPercent;
}

float CActuator::percent() const {
	auto val = percentUnbounded();
	val = MAX( val, 0 );
	val = MIN( val, 100 );
	return val;
}

void CActuator::setAlreadyAtPercent( float percent ) {
	m_currentPositionMs = int( m_fullTransitMs * (percent/100) );
}

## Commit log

2022-02-24 Updated README.md and renamed the box files
    [box Bottom.stl, boxBottom.stl]
2022-02-24 Add build outputs to the bin directory
    [boxBottom.stl, boxTop.stl]
2022-03-09 Code and box as installed in my boat
    [box.skp, boxBottom.stl, boxTop.stl]
2023-07-20 updated README, added some actuators

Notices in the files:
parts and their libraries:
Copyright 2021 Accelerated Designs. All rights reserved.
